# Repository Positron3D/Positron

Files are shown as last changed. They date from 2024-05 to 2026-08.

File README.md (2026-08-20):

  

<p align="center">
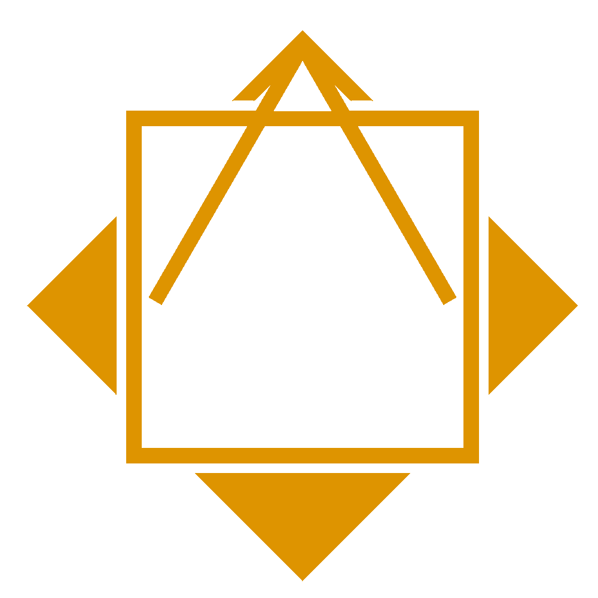
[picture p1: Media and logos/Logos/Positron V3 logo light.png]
   
</p>

---
# Positron V3.2.2
Designed by The Positron Team and LDO, the Positron V3.2 is the release version of the original Positron V3 design originally by Kralyn.

## The Positron Team
The Positron Team was founded by Kralyn and TheNomad after the release of the original Positron V3. Our team has worked closely with LDO to improve upon the original V3 design to make the entire unit more reliable, easier to assemble, and have a more elegant design as a whole.

## What is Positron
Positron is designed to be an ultra-portable printer. We have succesfully brought The Positron through major US International Airports without issue from TSA, the portability allows this printer to be easily brought along to any major event, remote workshop or maker space, job site, etc. If you have a need to bring a printer with you, The Positron may be the right printer for you.

## Why Positron?
As mentioned, we wanted an ultra-portable printer while we were in University. While travelling between our dorm and workshops, we often found the desire to bring our Printer with us, since we knew our own printers better than the community ones in the university.

We created the original V3 to achieve this goal, using what parts we had available to us at University. Then, when LDO reached out to us, we attempted to make the original V3 a production kit, but things that worked for our little team in University, didn't quite work out for mass production. As such, we spent 2 years working closely with LDO to make The Positron V3.2, an easy to assemble varient that is far more reliable for mass production.

We are extremely proud of this release, and we cannot wait for people to get their hands on the machines.

# Resources

### Klipper Configuration Files
The most up–to–date Klipper configuration files for setting up or updating the Positron are now in our [config repository](https://github.com/Positron3D/PositronConfig).
<!--#TODO: Remove "now" a few weeks after merge-->

### Mainboard / Daughterboard Schematics
For wiring & pin references, please see [LDO's Positron Hardware Repo](https://github.com/MotorDynamicsLab/PositronHardware/tree/master/PositronV3.2).

# Licenses


If you are manufacturing this 3D printer or a close derivative, please put `Positron Logo` visibily on your product and designate `Positron3D` as the inventor of this product. You can find the file inside the logos folder.

On any online postings for any Parts or Kits, please be sure to link back to this github page, as well as to Positron 3D's website.
`https://github.com/Positron3D/Positron`
`https://positron3d.com/`

If you made a profit from this design, please consider donating a portion to `Positron3D`. We will be exceedingly grateful.

***All hardware materials and designs provided here are licensed under the [CC-BY-SA-4.0](https://creativecommons.org/licenses/by-sa/4.0/) hardware license.
All documentation, including the Wiki, is under the Creative Commons [CC-BY-SA-4.0](https://creativecommons.org/licenses/by-sa/4.0/) license***.

<div align="center">
Open Licenses
</div>

## Exceptions to CC BY-SA 4.0 for LDO Motors – Positron 3D PCBs

The Positron 3D Team grants an exception to the CC BY-SA 4.0 license for PCBs developed for the Positron 3D printer and manufactured by LDO Motors under the following conditions:
1. Limited Scope: This exception applies only to PCB designs developed by the Positron 3D Team and manufactured by LDO Motors. All other components remain under CC BY-SA 4.0.
2. No ShareAlike Requirement: Modifications or derivatives of these PCBs do not need to be shared under CC BY-SA 4.0.
3. Commercial Use Restriction: Manufacturing and resale of these PCBs are limited to LDO Motors and authorized distributors. Personal, non-commercial use is permitted.
4. Attribution Requirement: Any use of these PCB designs must credit Positron 3D Team and LDO Motors per CC BY-SA 4.0.
5. No Warranty: The Positron 3D Team and LDO Motors provide the PCBs as-is, with no guarantees. Users assume all risks.

This exception ensures manufacturing consistency while maintaining open-source principles. For licensing inquiries, contact Positron 3D Team or LDO Motors.

[Top](#positronv3)

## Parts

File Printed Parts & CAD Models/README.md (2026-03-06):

# Before Printing - CALIBRATION
ABS and similar materials are prone to shrinking, changing the dimensions of the printed part from the original design.  If you have too much shrinkage, holes may not line up for screws, and parts may interfere with others.

We strongly recommend first printing the Calibration Test piece `calibration_test_100x30mm.stl` (Printed Parts & CAD Models\Calibration\) at 100% scale in the recommended print settings.

Measure the printed part (ideally with at least inexpensive calipers).  The part should be as close to 100mm in length and 30mm in length as possible.  

Adjust the scale in the slicer until the printed part measures 100mm in length and 30mm in width.  **Use this updated scale for the rest of the printed parts.**

example: Printing the calibration piece at 100.5% yields a measured printed part of 100x30mm; use 100.5% to scale all other printed parts by X/Y/Z in the slicer.

NOTE: The 3mf files in the **\#Pre-Sliced Plates folder** default to 101% scale.  This may or may not be appropriate for your printer!  Select all the parts and change the scale to the scale percentage you determined above before slicing.

# Version
Current Release Printed Parts = Positrion V3.2.2 (includes LDO Batch 3; current as of 2026-03-06).

# Directory
## CAD Files
Exactly what it says - these are the CAD files of the Positron V3.2

## Current Release Printed Parts
If you wish to build a stock Positron, this is how you do it.

## Experimental Release Printed Parts
These are various parts in the stage of testing, we are experimenting with these as potential Release Candidates.

If testing goes well, these will likely be adopted as official design revisions.

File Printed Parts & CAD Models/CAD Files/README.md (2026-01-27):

# Updated 2026-01-26
The CAD files have been cleaned up, color/material assigns in the Fusion files (f3d).  All subassemblies have been re-organized and re-exported into the Subassemblies folder.

The files have a _YYYY-MM-DD suffix noting the date of export.

# Live (Web) CAD Viewer
The initial LDO Kit Release Live Fusion Model can be [viewed here](https://a360.co/4dAXmJX) (2024-08-23 version).

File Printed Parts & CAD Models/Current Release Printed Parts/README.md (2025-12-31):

# Positron v3.2 Printed Parts
Hello - all of these folders are what is required to build your Postiron.

In each folder, you will find a readme, this will act as a general Key for the naming of the files, as well as a spot where we've added advisories for some parts. This is as simple as informing you if a part will not be seen from the exterior, if a part will be closely intact with a high temperature item such as a motor, or if a part is recommended to be non-conductive for electrical isolation.

Please note that the folders here are grouped by assembly, and not by recommended order of assembly. Please be sure to follow the guides provided on our wiki.

# Material needed
 - 198.51g for Primary
 - 170.57g for Accent

# Recommended Print Settings

 - We recommend printing all parts in ABS or ASA
 - [We're copying Voron's homework;](https://docs.vorondesign.com/sourcing.html#print-settings)
    - Layer height: 0.2mm
    - Extrusion width: 0.4mm
    - Infill percentage: 40%
    - Infill type: grid, gyroid, honeycomb, triangle, or cubic
    - Wall count: 4
    - Solid top/bottom layers: 5
    - Supports: NONE

ABS or ASA is the recommended filament for most parts, PLA and PETG can be used for accent pieces, but please only do so at your own discretion.

## Important Note
These files are not pre-scaled as modern slicers have a shrinkage factor built in, please be sure to scale your parts accordingly. If you are unsure, try scaling parts by 100.5%

# Example Renders
Below are renders we generated. For reference between "Primary" and "Accent" colors;
 - Primary Colors; Extruder, Panels, Main Hotend Body
 - Accent Colors; Control Panel, Vents, End Caps.
 - Any Colors; Non visible parts that will not be seen in the final build.

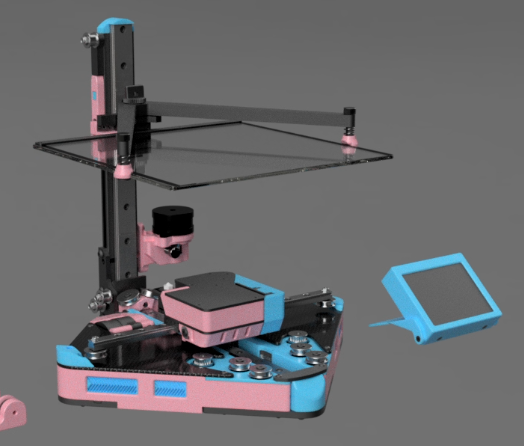
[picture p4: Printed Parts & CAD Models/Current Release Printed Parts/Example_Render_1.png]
Example Render 1

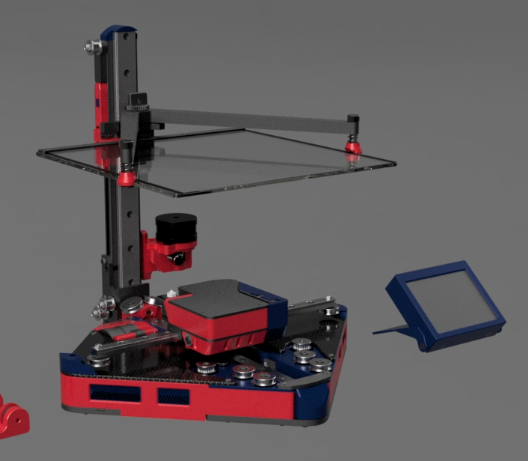
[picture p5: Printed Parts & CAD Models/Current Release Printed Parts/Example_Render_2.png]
Example Render 2

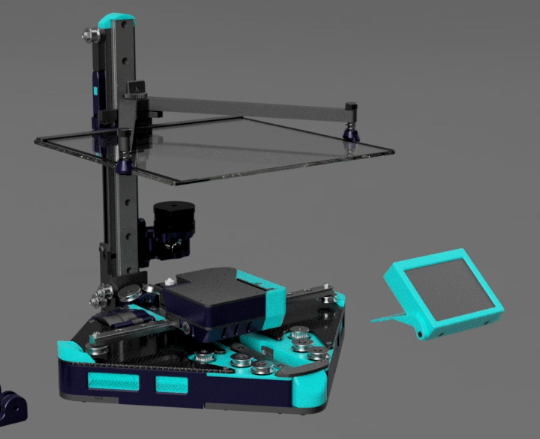
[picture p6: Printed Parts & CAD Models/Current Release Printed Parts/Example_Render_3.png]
Example Render 3


# FILE NAME KEY:
`Part Name - Quantity - Recommended Color - Notes`

### Example 1;
`Bed_Cable_Guide - 1x - Accent`  

This is the `Bed_Cable_Guide`, you need to print One of them, recommended in an accent color.

### Example 2;
`Z_PCB_Spacer - 1x - Any - Non-Conductive`

This is the `Z_PCB_Spacer`, you need to print One of them, you can use any color, and must not be conductive.

# Questions or Comments
Please feel free to join our [Discord](https://discord.gg/positron) to help with any feedback. We appreciate any and all feedback that can help us better improve our designs.

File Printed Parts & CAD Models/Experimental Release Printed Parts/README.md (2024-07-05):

# Experimental Printed Parts
## What are Experimental Parts
Experimental Parts are parts that The Positron team is looking to implement as a full update, replacement, or change to the overall design.

Experimental Parts are in the process of being tested by any and all volunteers who wish to participate.

The participation of Experimentations are tracked in the Discord.

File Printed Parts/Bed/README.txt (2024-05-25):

KEY:
Part Name - Quantity - Recommended Color - Minimum Material Type - Notes

Example 1;
Bed_Cable_Guide - 1x - Accent - PLA

This is the Bed_Cable_Guide, you need to print One of them, recommended in an accent color, and at the minimum in PLA.

Example 2;
Z_PCB_Spacer - 1x - Any - ABSorASA - Non-Conductive

This is the Z_PCB_Spacer, you need to print One of them, you can use any color, at the minimum in ABS or ASA, and must not be conductive.

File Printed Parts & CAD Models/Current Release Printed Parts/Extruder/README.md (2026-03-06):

# IMPORTANT FOR THIS FOLDER

These are the printed parts for the original / OLD Extruder v1.  The [LDO Assembly Guide](https://ldomotion.com/guides/1---positron-v32---extruder) currently shows the instructions for this.

We do strongly suggest instead using the v2 Extruder if possible.  It is substantially more reliable and performant.

An assembly guide for the Extruder v2 is in progress, but you may find it helpful to use the [Positron3D CAD Viewer](https://cad.positron3d.com/?model=Positron_v3.2.2) and expand into the Extruder_v2 to see how it goes together.

## BOM
All needed parts are included with the LDO Positron Kit (there are plenty of extra fasteners):
- M2x10 Self Tapping Screw (Quantity: 2)
    - Used to attach the Z Endstop Switch to the `extruder_v2_main_body`)
- M3x25 BHCS (Quantity: 3)
    - 1x goes from the bottom through `extruder_v2_bottom_plate` and `extruder_v2_main_body` into a M3x5x4 Heatset Insert in `extruder_v2_motor_plate`.
    - 2x go through the bottom of `extruder_v2_main_body` into the LDO Pancake Stepper.
- M3x8 BHCS (2x)
    - 2x go through the bottom of `extruder_v2_bottom_plate` into M3x5x4 Heatset Inserts in `extruder_v2_main_body_*`.
- M3x5x4 Heatset Insert (Quantity: 4)
    - 1x goes into the bottom of `extruder_v2_motor_plate` (see above).
    - 2x go into the bottom of `extruder_v2_main_body_*` (see above).
    - 1x goes into the side of `extruder_v2_guidler`.
- M4 Hex Nut (Quantity: 2)
- M4x10 BHCS (Quantity: 2)
- EITHER: M3x35 SHCS or M3x35 BHCS OR the silver M3 Thumbscrew (see note below) (Quantity: 1)
    - This goes through the spring, through the washer, and into the front of `extruder_v2_main_body` and into the M3x5x4 Heatset Insert on `extruder_v2_guidler` as the tensioning mechanism.
- Extruder BMG Spring
- Washer

## Extruder Main Body Notes!
There are two versions for this part:  

Option A)
If you would like to use a M3x35 SHCS (Socket Head) or M3x35 BHCS (Button Head) as the tension fastener, use the `extruder_v2_main_body_m3x35.stl`.  Once tension is set, it generally never needs adjustment, so the smaller form factor is nice.

Option B)
If you would like to use the Silver M3 Thumbscrew supplied in the LDO Kit (originally used with the old Extruder V1), use `extruder_v2_main_body_m3thumbscrew.stl`.

Print information for the new Extruder v2 is found below:

## Colors and Naming
You will see two options;
1. If there is a `[a]` at the start of the filename, this denotes it can be printed with an accent color
    - This is a secondary, often complimentary color, and will help your build pop.
2. If there is no prefix at the start of the filename, this denotes it can be printed with the main color
    - This is the majority of the parts of the build.

Of course, these are just color coordination suggestions, please experiment and have fun!

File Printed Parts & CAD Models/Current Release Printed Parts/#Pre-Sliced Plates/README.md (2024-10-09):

# Pre-Sliced Plates
Hey, these plates aren't updated as often as the other folders are.

While these are here for convenience, we ask that you read through the other folders and update your parts accordingly.

Thank you.

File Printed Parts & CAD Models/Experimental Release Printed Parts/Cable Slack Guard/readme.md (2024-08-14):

# Cable Chain Experiment
We understand that some users have had issues with the Cables and Bowden getting caught on the X Rail during prints. 

This can be printed in anything, and has been tested without issue with PLA.

This uses the heatset insert that the original Bowden Guide, and the original screw to attach it.

# Printing
Default Strength Profiles work well for this, must use a 0.4 nozzle and be able to print walls that are 0.5mm thin.

# Assembly

Insert the heatset insert to the Toolhead Holder, and screw that into the Toolhead.

Slide the Links onto Bowden Tube, and place the XT30 cable into the clip side.

Lock the clips in, and push in the Band. This will secure the clips and will ensure they don't open.

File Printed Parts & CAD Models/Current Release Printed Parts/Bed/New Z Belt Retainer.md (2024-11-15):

# New Z Belt Retainer
Insert Two M3x10 SHCS into the back of the block, this is for added strength.
    - Not through the screw holes that go all the way through the block
Attach to the Z Carriage as normal

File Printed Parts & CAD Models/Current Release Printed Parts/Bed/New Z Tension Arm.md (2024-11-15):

# Z Tension Arm Assembly
This is now the default for Batch 3 forward. If you have a Batch 1 or 2 kit, you have all the parts to build this.

# General Instruction/Notes
M3 10mm OD washer and M3x12 BHCS or a wafer head for the pivot.
The previously used M4x10 BHCS and an M4 hex nut for the stop.
Place the ball bearing in the Z_Tension Arm, followed by the spring
Use an hex driver to compress the spring towards the ball bearing, and slide in the Tension Plug.

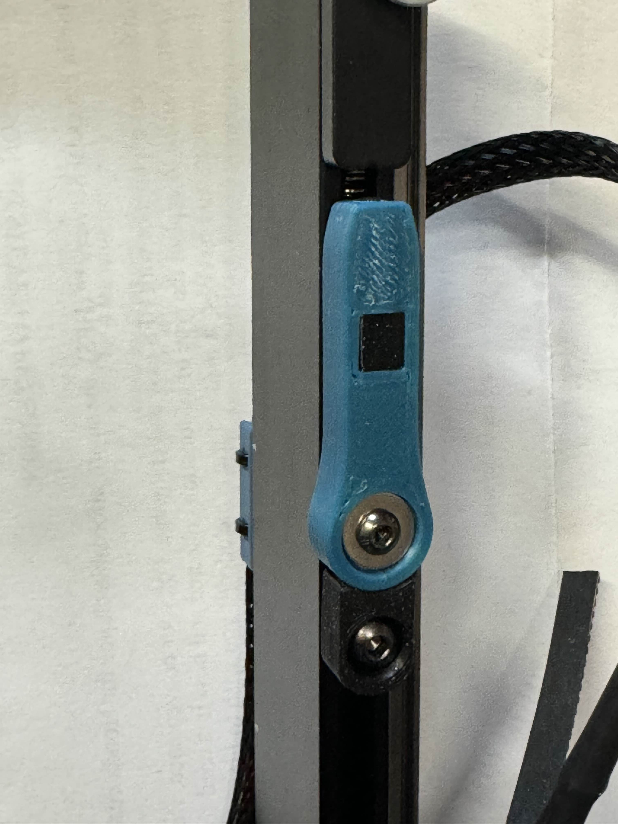
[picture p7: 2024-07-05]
Printed Parts & CAD Models/Current Release Printed Parts/Bed/New Z Tension Arm.jpg

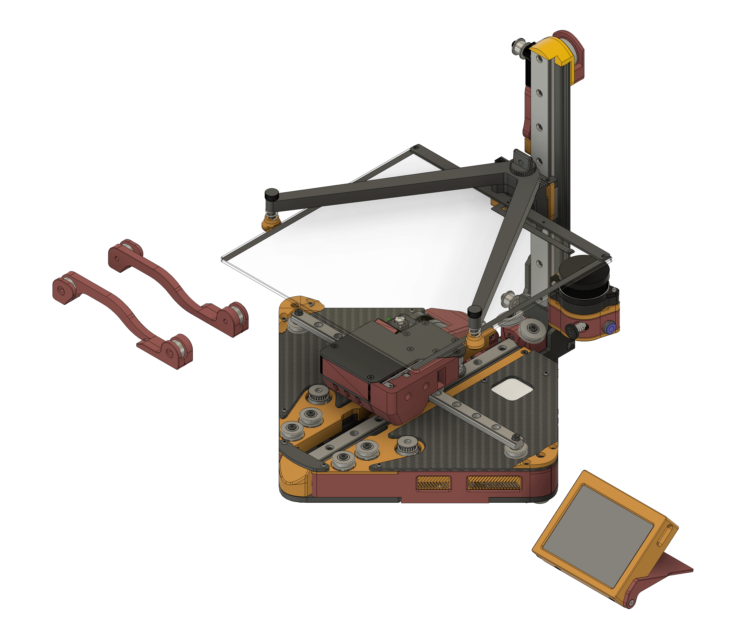
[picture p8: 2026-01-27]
Printed Parts & CAD Models/CAD Files/PositronV3.2.2_2026-01-26.png

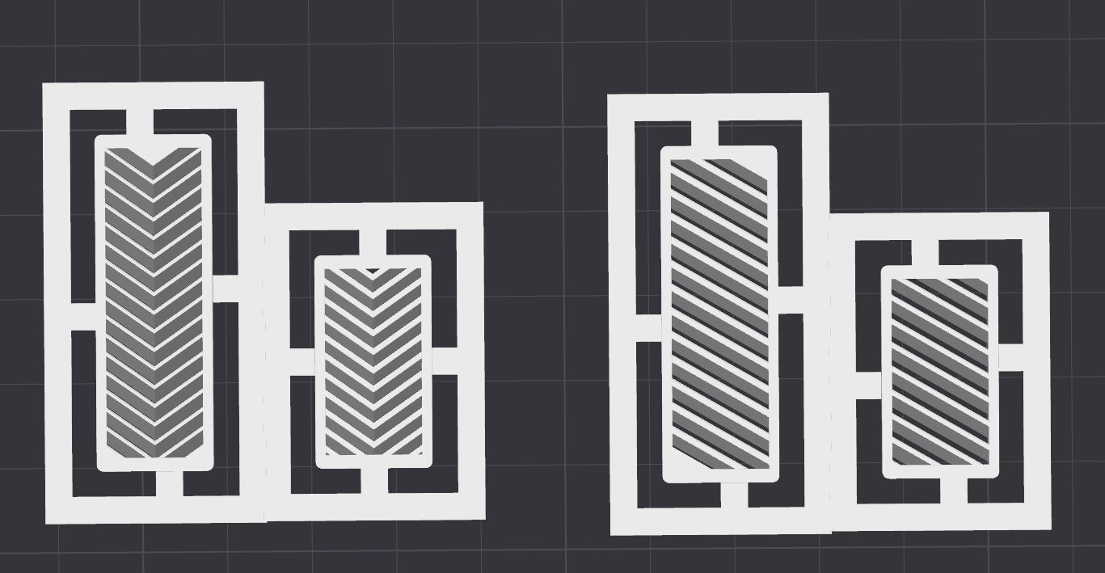
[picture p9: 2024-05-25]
Printed Parts & CAD Models/Current Release Printed Parts/Panels/Vent Grills/Style_Compare.png

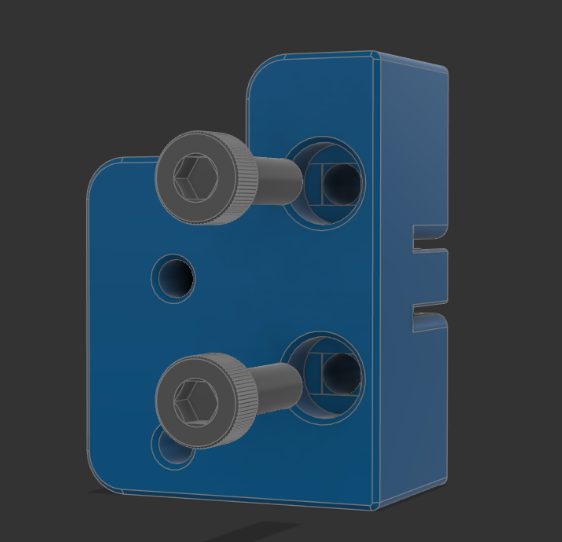
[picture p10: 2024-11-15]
Printed Parts & CAD Models/Current Release Printed Parts/Bed/Z_Belt_Retainer - Added M3x10.png

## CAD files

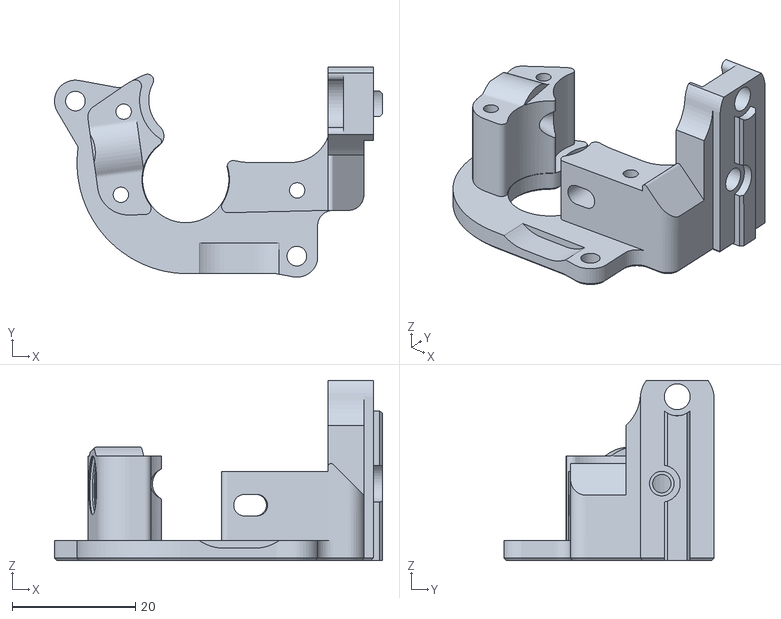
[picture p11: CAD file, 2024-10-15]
Printer Mods/Extruder - Threaded Bowden Coupler/M10 Bowden Coupler/Extruder_Main_Body - 1x - Primary - M10 Bowden - V1.1.stl
53.2 x 34.1 x 29.2

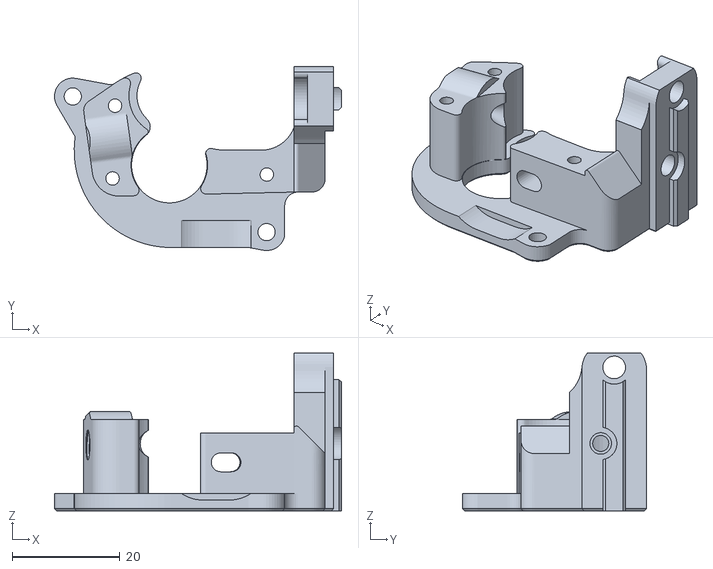
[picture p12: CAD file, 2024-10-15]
Printer Mods/Extruder - Threaded Bowden Coupler/M6 Bowden Coupler/Extruder_Main_Body - 1x - Primary - M6 Bowden - V1.1.stl
53.2 x 34.1 x 29.2

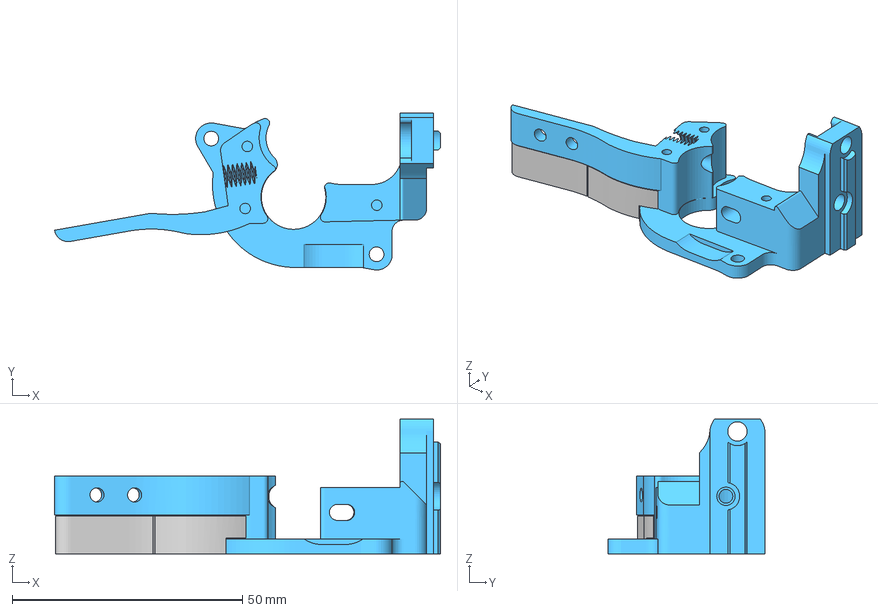
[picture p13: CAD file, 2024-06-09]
Printer Mods/Cable Chain Mod/Extruder Main Body - Cable Chain - V0.1.3mf
83.9 x 34.1 x 29.3 mm
Extruder Main Body
Included Support (1)
Included Support

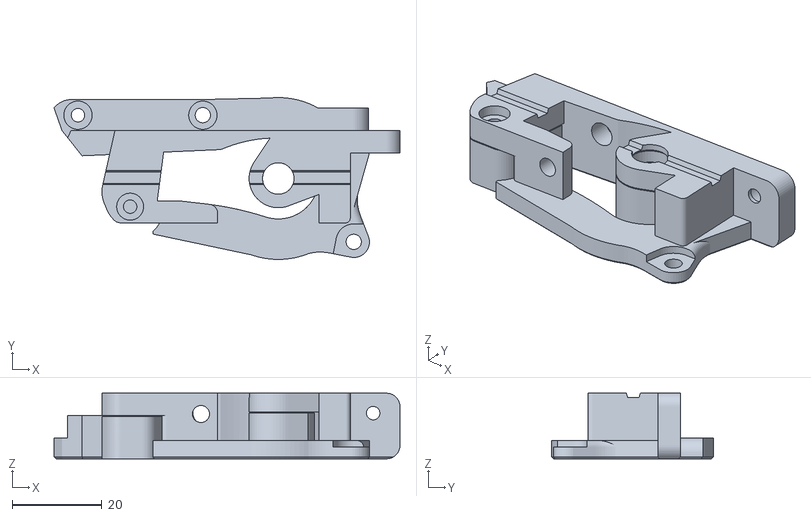
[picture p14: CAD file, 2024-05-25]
Printed Parts & CAD Models/Current Release Printed Parts/Z Drive/Z_Drive_Main_Body - 1x - Primary - HS - V1.0.stl
76.9 x 36.0 x 14.6

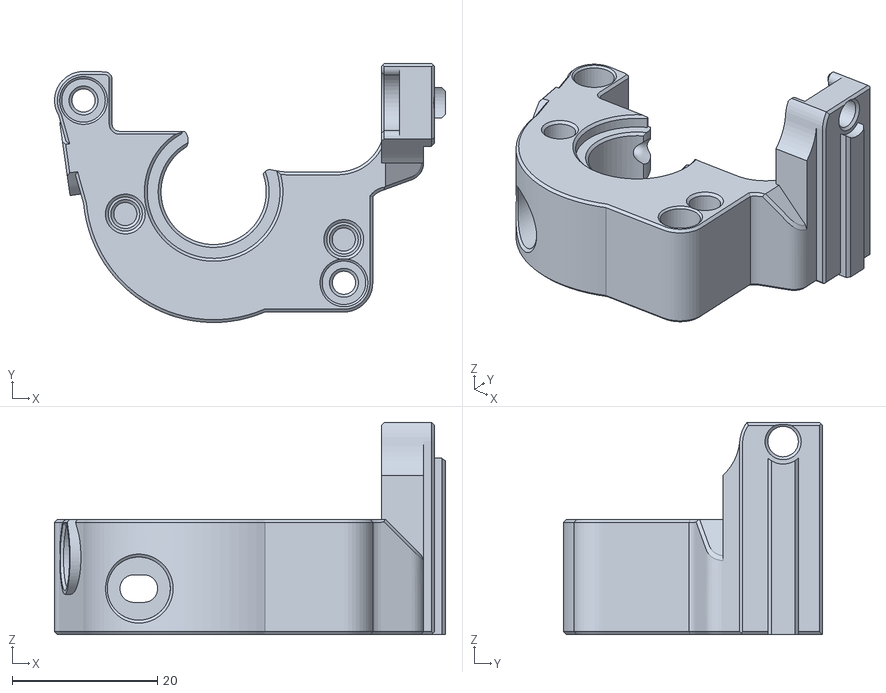
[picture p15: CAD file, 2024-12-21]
Printed Parts & CAD Models/Current Release Printed Parts/Extruder/extruder_v2_main_body_m3x35.stl
53.9 x 35.7 x 29.3

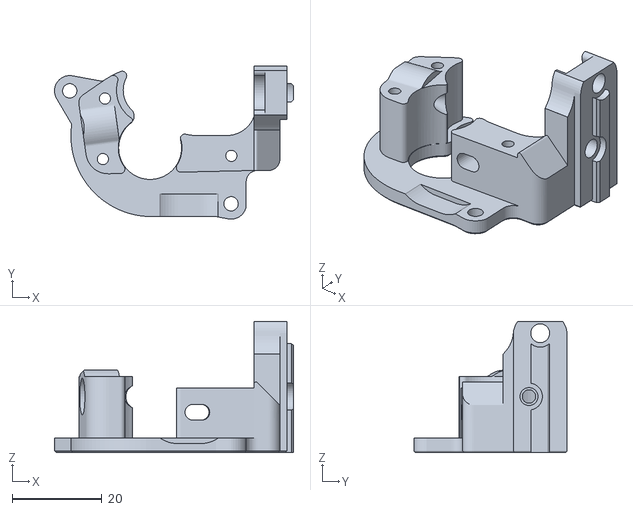
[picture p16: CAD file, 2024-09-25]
Printed Parts & CAD Models/Current Release Printed Parts/Extruder/Extruder_Main_Body - 1x - Primary - V1.1.stl
53.2 x 34.1 x 29.2

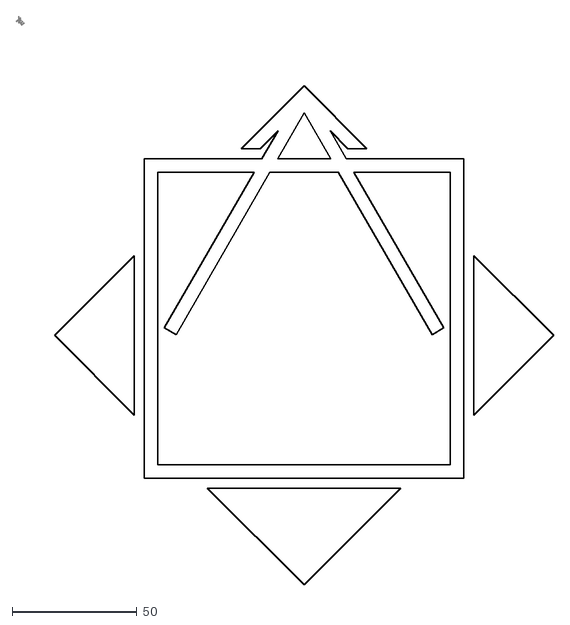
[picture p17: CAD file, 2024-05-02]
Media and logos/Logos/Positron V3 Logo v2.dxf
214.9 x 227.5

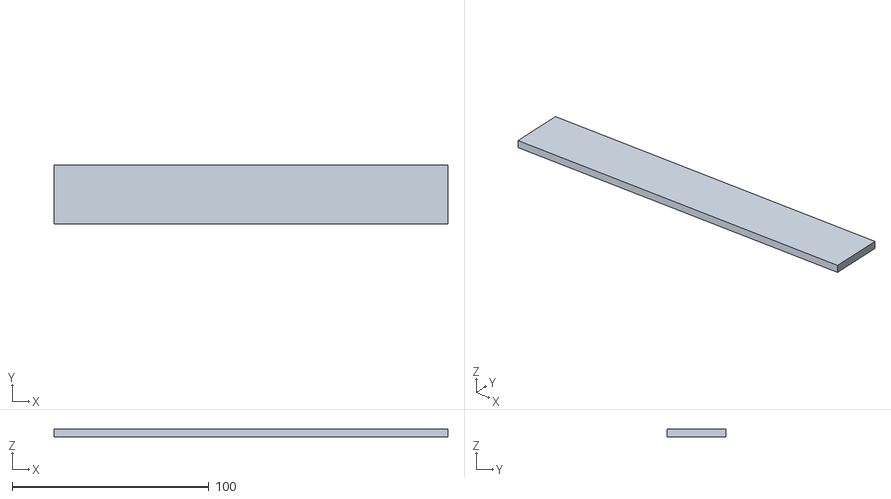
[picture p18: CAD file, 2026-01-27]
Printed Parts & CAD Models/Calibration/calibration_test_200x30mm.stl
200.0 x 30.0 x 4.00

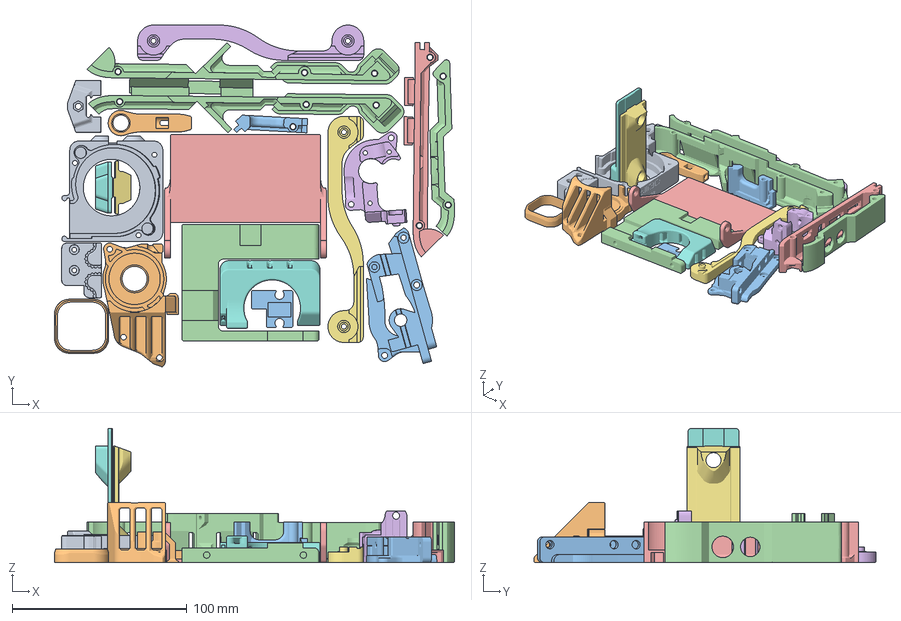
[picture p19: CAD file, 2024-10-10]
Printed Parts & CAD Models/Current Release Printed Parts/#Pre-Sliced Plates/PrusaMK4S-PRIMARY-ASA.3mf
228.6 x 195.5 x 76.8 mm
Z_Belt_Retainer_Alternative.stl
Z_Tension_Arm.stl
Z_PCB_Spacer - 1x - Any - Non-Conductive - V1.0.stl
Back_Plate - 1x - Primary - Non Conductive - HS - V1.0.stl
Cover_Stand - 1x - Primary - V1.0.stl
Extruder_Main_Body - 1x - Primary - V1.1.stl
Light_Bar_Bracket_Front - 1x - Any - V1.0.stl
Light_Bar_Bracket_Rear - 1x - Any - V1.0.stl
Rear_Idler_Tensioner_Block - 1x - Primary - HS - V1.0.stl
LED_Cluster_Retainer - 1x - Any - Heat Warning - V1.0.stl
Rear_Cable_Panel - 1x - Primary - HS - V1.0.stl
Side_Panel_Back_Left - 1x - Primary - HS - V1.0.stl
Side_Panel_Back_Right - 1x - Primary - HS - V1.0.stl
SpoolHolder_B - 2x - Primary - V1.0.stl x 2
Toolhead_Belt_Retainer_Block - 1x - Primary - HS - V1.0.stl
Part_Fan_Enclosure_Alt - 1x - Primary - HS - V1.3 - Olli3D - Housing.stl
Z_Drive_Outer_Housing - 1x - Primary - HS - V1.1.stl
Z_Drive_Main_Body - 1x - Primary - HS - V1.0.stl
Merged

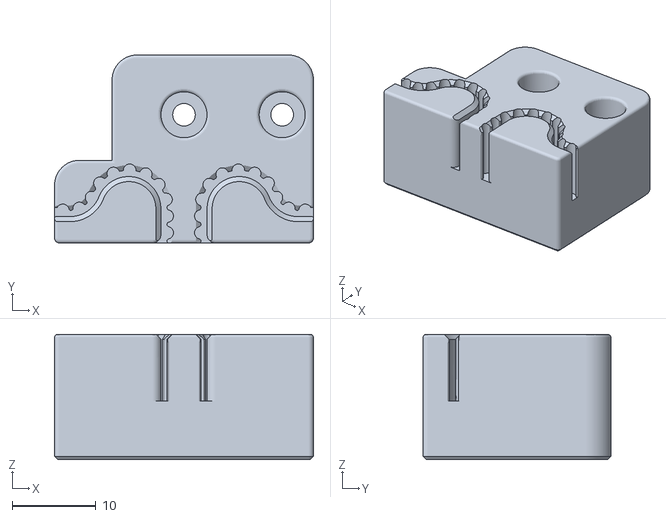
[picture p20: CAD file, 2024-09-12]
Printed Parts & CAD Models/Current Release Printed Parts/Bed/Z_Belt_Retainer - 1x - Primary - V1.3.stl
31.0 x 22.5 x 15.0

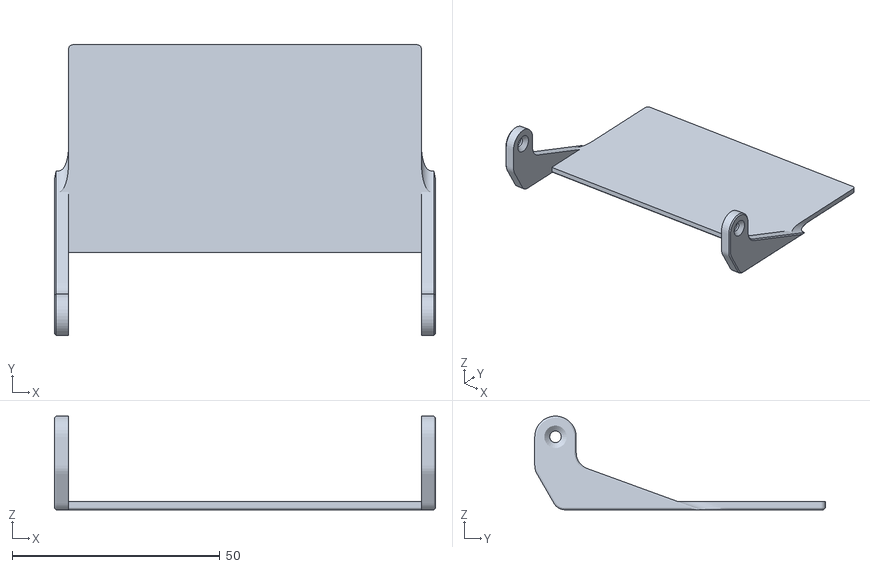
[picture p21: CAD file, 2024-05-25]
Printed Parts & CAD Models/Current Release Printed Parts/Controller/Cover_Stand - 1x - Primary - V1.0.stl
91.8 x 70.0 x 22.6

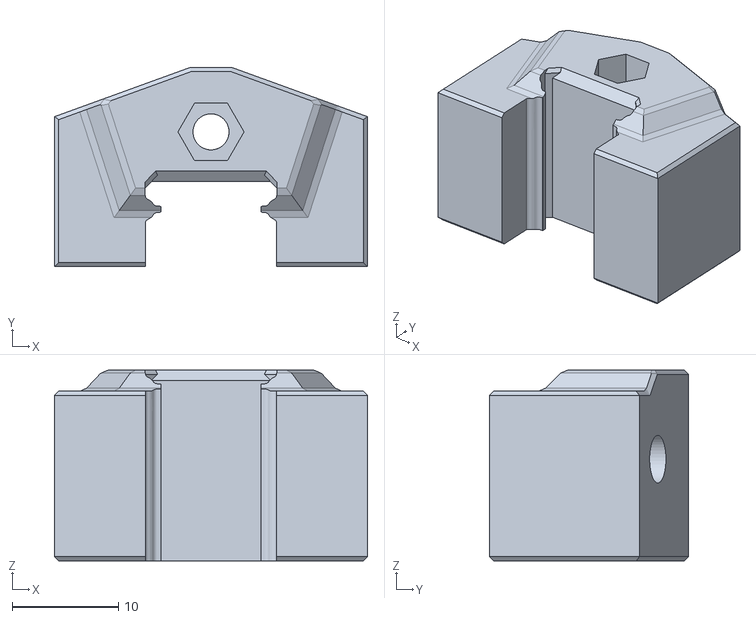
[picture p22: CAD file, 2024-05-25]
Printed Parts & CAD Models/Current Release Printed Parts/Motion/Rear_Idler_Tensioner_Block - 1x - Primary - HS - V1.0.stl
29.5 x 18.8 x 18.0

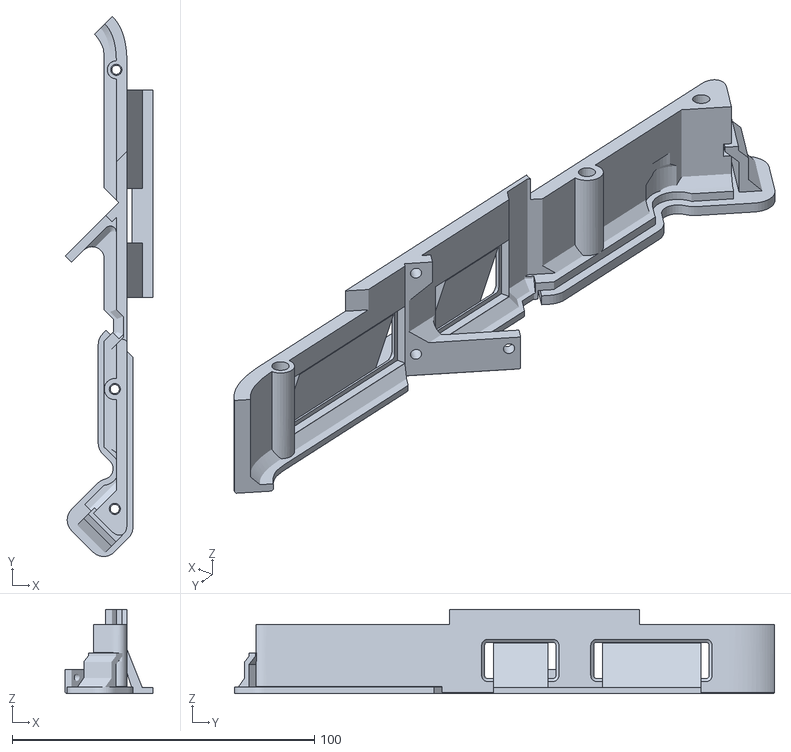
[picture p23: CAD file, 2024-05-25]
Printed Parts & CAD Models/Current Release Printed Parts/Panels/Side_Panel_Front_Left - 1x - Primary - HS - V1.0.stl
29.1 x 178.5 x 27.9

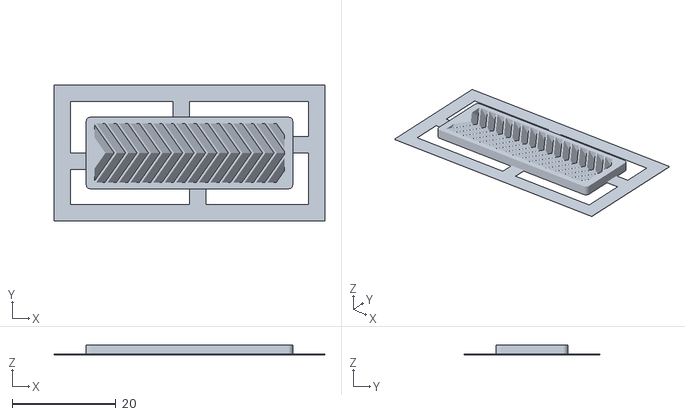
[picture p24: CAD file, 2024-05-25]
Printed Parts & CAD Models/Current Release Printed Parts/Panels/Vent Grills/Fishbone/[V]Fish_Bone_Grill_Large - 2x - Accent - V1.0.stl
52.2 x 26.2 x 2.00

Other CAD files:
Printed Parts & CAD Models/Current Release Printed Parts/Panels/Vent Grills/Slanted/[V]Slanted_Grill_Small - 2x - Accent - V1.0.stl
Printed Parts & CAD Models/Current Release Printed Parts/Panels/Vent Grills/Template Grill Frames.step
Printed Parts & CAD Models/Current Release Printed Parts/Spool Holder/SpoolHolder_C - 2x - Accent - V1.0.stl
Printed Parts & CAD Models/Current Release Printed Parts/Toolhead/Part_Fan_Enclosure - 1x - Primary - HS - V1.4 - Olli3D - Housing.stl
Printed Parts & CAD Models/CAD Files/PositronV3.2.2_2026-01-26.f3d
Printed Parts & CAD Models/CAD Files/Subassemblies/Extruder_V2_CAD.f3d
Printed Parts & CAD Models/CAD Files/Subassemblies/extruder_v2_main_body_m3thumbscrew.step
Printed Parts & CAD Models/Current Release Printed Parts/#Pre-Sliced Plates/PrusaMK4-ACCENT-ASA.3mf
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

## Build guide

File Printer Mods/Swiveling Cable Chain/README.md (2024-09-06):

# Swiveling cable chain mod

This mod adds a swiveling attachment to the extruder. This makes it possible to fold the printer
even with the cable chain still attached. The Pelican-style case that the LDO Positron ships with
can also be modified to fit the folded printer with the cable chain sticking out.

## Extra hardware required

  - 2x M2.5 BHCS 6mm bolts
  - 1x MF-148-ZZ bearings (the same type of bearing that is already in the Positron BOM)

## Printing

Print the provided STL file by splitting it into objects and rotating the pieces into the right orientation.

## Assembly

  - Push the plug through the bearing, and attach the arm that will hold the cable chain to the plug using both M2.5 6mm bolts.
  - Take this assembly and slot it into the niche for the bearing into the other two parts.
  - Possibly clear out the filament path using a 2mm drill bit, if there is anything obstructing it.
  - Assemble using the same extruder-side pieces as in the original cable chain mod.

## Photos

Open:

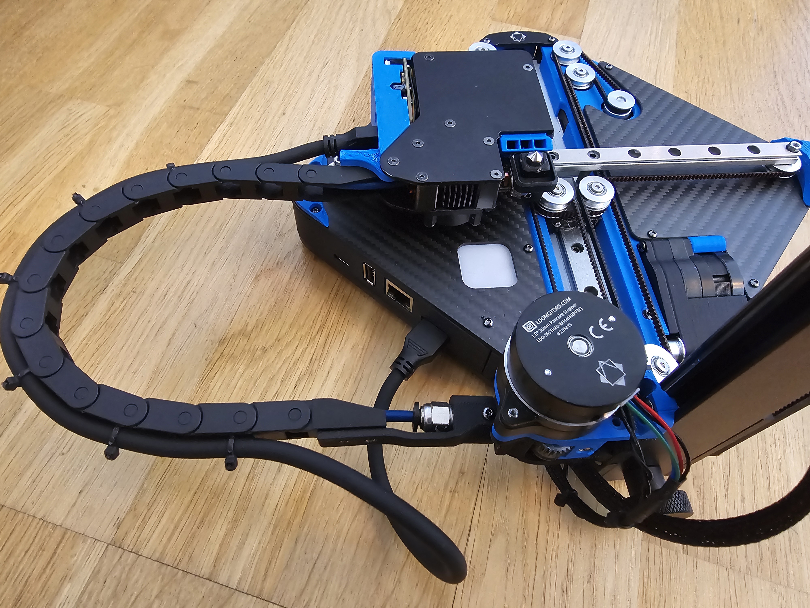
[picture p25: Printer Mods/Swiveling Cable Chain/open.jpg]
open position


Folded:

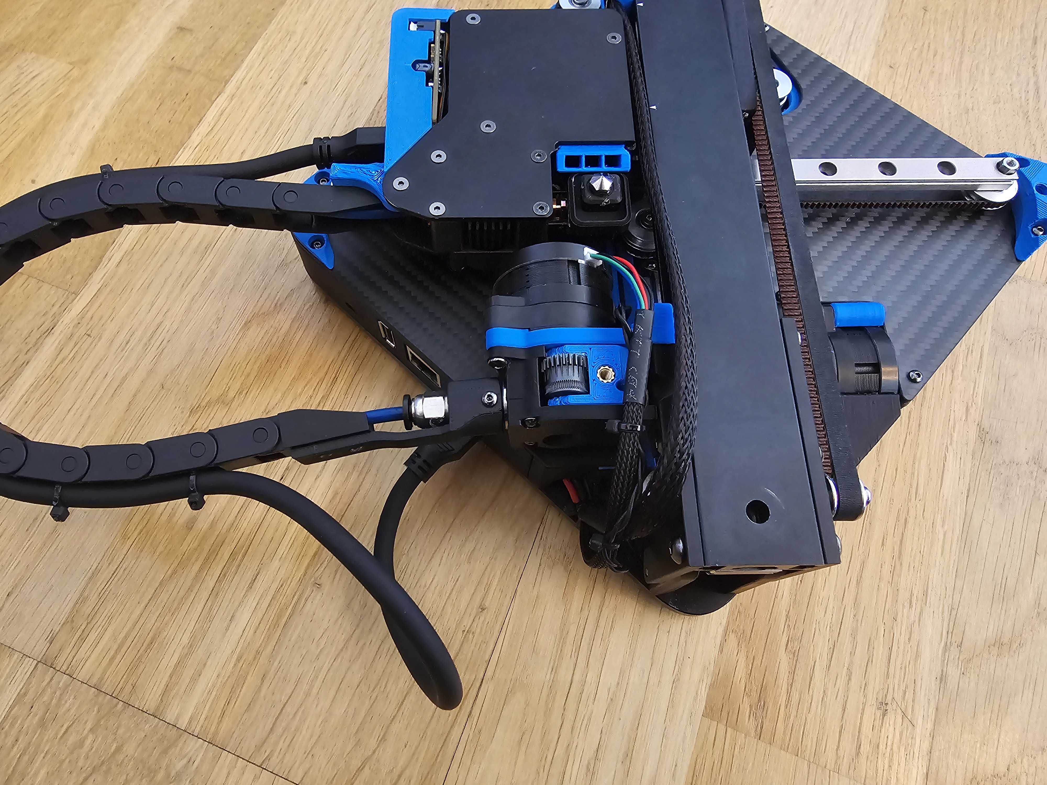
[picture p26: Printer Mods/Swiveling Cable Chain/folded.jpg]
folded positron


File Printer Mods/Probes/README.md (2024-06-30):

# Welcome to the Probes Mod Folder
No, this is not for alien abductions.

This is for any custom probe mods people wish to add to the Positron.

We have attached the first 'universal' mount system.

The current philosophy of the probe is to give the Positron a Magnetic mount of sorts for various probes.

We've included the STEP files here, and we encourage our community to build upon this, and potentially even design a method of docking probes.

Have fun.

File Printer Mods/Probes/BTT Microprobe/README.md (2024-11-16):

# Positron v3.2 - BTT Microprobe Mod
This mod allows for a Microprobe to be mounted to the Toolhead.

For Wiring reference, please see [LDO's Positron Hardware Repo](https://github.com/MotorDynamicsLab/PositronHardware/tree/master/PositronV3.2).

This mod uses some existing hardware, and mounts to the Toolhead's Heatsink. This part is very thin to allow for maximum clearance between the toolhead and the extruder. Please test your setup to ensure there is no collision.

The Servo cable is plugged into the SERVOS pins on the MCU - GPIO29

The Probe cable is plugged into the TH0 pins on the MCU - GPIO27
> Note - TH0 / GPIO27 is unused in stock configuration.

# Required Hardware
- 2x m2.5x10 for Probe Mount
- 12x 3x2mm Magnets
- 4x M2.5x6 BHCS (Included in Positron Kit)
- JST PH 2Pin Female + JST PH 3Pin Female to JST GH 5Pin Female Connector (**not** included with BTT Microprobe)

# Installation Instructions
1. Glue 6x 3x2mm Magnets into the `Probe_Heatsink_Mount`
2. Glue 6x 3x2mm Magnets into the `BTT_Microprobe Probe Harness`
3. Ensure the Magnet polarities match to allow the two parts to magnetically mount.
4. On the underside of the toolhead, remove the 4x M2.5x6 BHCS screws holding the heatsink to the bottom plate.
5. Using the screws you just removed, mount the `Probe_Heatsink_Mount` to the underside of the bottom plate, using the same holes as before.
6. Mount the BTT Microprobe to the `BTT_Microprobe Probe Harness`
7. Test and make sure the two components can magnetically couple, and decouple.

# Recommended Print Settings

 - We recommend printing all parts in ABS or ASA
 - [We're copying Voron's homework;](https://docs.vorondesign.com/sourcing.html#print-settings)
    - Layer height: 0.2mm
    - Extrusion width: 0.4mm
    - Infill percentage: 40%
    - Infill type: grid, gyroid, honeycomb, triangle, or cubic
    - Wall count: 4
    - Solid top/bottom layers: 5
    - Supports: You should be able to get away with none, but you may need a few as there are a few major overhangs.

ABS or ASA is the recommended filament for most parts, PLA and PETG can be used for many accent pieces, but please only do so at your own discretion.

# Questions or Comments
Please feel free to join our [Discord](https://discord.gg/mGDkYZtyNY) to help with any feedback. We appreciate any and all feedback that can help us better improve our designs.

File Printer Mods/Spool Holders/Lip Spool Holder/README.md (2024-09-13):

# Lip Spool Holder

A simple spool holder that replaces the Z column keystone that requires no setup, but only works with spools that have an inner lip.

It requires a M3 heatset insert and 3 × 6-10mm M3 Flat Head Socket Screws (FHSS) which can likely be sourced from spares includes with thte Positron kit. The bearing is not included, but it is a common 608 bearing commonly found in skateboards or rollerskates.

The mod is printed in two parts, flat and without supports.




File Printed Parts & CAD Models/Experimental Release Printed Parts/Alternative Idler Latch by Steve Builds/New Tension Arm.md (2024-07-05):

# Notice
This is a piece that SteveBuilds helped us redesign, we're still testing it out, but it's a bit more elegant of a design.

# General Instruction/Notes
M3 10mm OD washer and M3x12 BHCS or a wafer head for the pivot.
The previously used M4x10 BHCS and an M4 hex nut for the stop.

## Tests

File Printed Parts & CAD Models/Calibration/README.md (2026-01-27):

# Before Printing - CALIBRATION
ABS and similar materials are prone to shrinking, changing the dimensions of the printed part from the original design.  If you have too much shrinkage, holes may not line up for screws, and parts may interfere with others.

We strongly recommend first printing the Calibration Test piece `calibration_test_200x30mm.stl` (Printed Parts & CAD Models\Calibration\) at 100% scale in the recommended print settings.

Measure the printed part (ideally with at least inexpensive calipers).  Input the length of the part into the formula below to get your shrinkage scale percentage:

Scale Percentage = (200 / measured_length) * 100

Example: 
Printed calibration piece measured 198.2mm in length.
Scale Percentage = (200 / 198.2) * 100
Scale Percentage = 100.9%

**Use this updated scale for the rest of the printed parts.**

example: Printing the calibration piece at 100.5% yields a measured printed part of 100x30mm; use 100.5% to scale all other printed parts by X/Y/Z in the slicer.

NOTE: The 3mf files in the **\#Pre-Sliced Plates folder** default to 101% scale.  This may or may not be appropriate for your printer!  Select all the parts and change the scale to the scale percentage you determined above before slicing.

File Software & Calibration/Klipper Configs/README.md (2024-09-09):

## The Positron configuration files have moved: [Positron3D/PositronConfig](https://github.com/Positron3D/PositronConfig)

To help make getting the latest configs easier[^1], we've flown the Klipper configuration files over to [Positron3D/PositronConfig](https://github.com/Positron3D/PositronConfig) so you can easily download just the latest configurations without having to download the whole repository or individual files, or copy-paste the contents of the files.

We will also be able to have alternate configuration sets in the future for common mods or experimental tweaks, so stay tuned. In the meantime, happy printing^2

<p align="center">
   
</p>

[^1]: Except for this time I guess, given you're here...
[^2]: Though not on planes, only shameful printing on planes.[^9000]
[^9000]: I just figured out how to use these footnotes so I'm abusing it

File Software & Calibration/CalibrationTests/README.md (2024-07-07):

# PLEASE READ ME
This is a selection of calibration tests custom made for the Positron v3.2

# The files
## Positron_orca_BedLevel.3mf

Uses Orca Slicer with default Positron V3.2 machine settings.

This is a test file for helping with bed leveling created by joescalon.

It has been tuned for PLA, and prints by object.

First object is back center for testing z-offset.

Second and Third are front corners for testing level.

Last is the Positron Logo in the center for final level test.

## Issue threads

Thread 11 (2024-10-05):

XT30 connector loosening over time

nomadsgalaxy, 2024-10-05:
Multiple Volunteers Wanted;
Rob Volunteered
Nem Volunteered

Ideas;
Latching Design
Screwed Design
or Slot Design

Killajoedotcom, 2024-10-07:
Hell, I'll volunteer as well.

nomadsgalaxy, 2024-10-07:
> Hell, I'll volunteer as well.

Assigned - feel free to tinker. The idea is to come up with something easy to print that can lock the connector head in but be easily removed.

nomadsgalaxy, 2025-01-05:
Fix for Batch 1 & 2: https://thangs.com/designer/TechJeeper%20Designs/3d-model/Positron3D%20Toolhead%20Cover%20with%20Cable%20Clip-1236899

Batch 3 has new cable design.

Closed 2025-01-05.

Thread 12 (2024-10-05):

Bed Connector Revision (Printed Parts)

nomadsgalaxy, 2024-10-05:

smiksky, 2024-11-11:
Originally titled "Bed Connector Revision (Printed Parts)", but this isn't an issue or contribution at this point

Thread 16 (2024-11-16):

Links from LDO assembly guide lead to 404 pages

orcinus, 2024-11-16:
This is seriously unprofessional.
You can't just yank files that are actively linked by the up-to-date, web published guide.
Some of them are now moved into "old parts" folders.
Some (e.g. Z Idler Latch Plug) are seemingly completely missing.

This is ridiculous.

nomadsgalaxy, 2024-11-16:
Hi - The Positron team does not maintain the LDO guide, and we are very closely working with them to update the guide. But in order to do so, the github has to first be updated.

If you need assistance, please join our Discord, for the mentioned parts, we just announced their update last night. We'd be happy to assist with any guidance needed.

orcinus, 2024-11-16:
Thanks for the support and help.

This isn't so much about who maintains what - it's about not breaking links and managing the repo.
You can create a branch, with a "frozen" configuration, that outside resources link to, and continue working on master branch with further improvements. Or you can do the opposite - keep master frozen as a "production" branch, and keep further developments in a development branch until the ecosystem is ready for a merge.

I understand LDO is a separate team, but to my knowledge, that is the only publicly available guide you have. I hate telling people what to do and how to do it, but your team should take care of it too, not just bounce the ball back.

Also, Discord is a black hole for any open source project. Finding anything in Discord is a nightmare, it's bad for archival, it's bad for discoverability, and it's bad for pretty much anything other than discussion. It *should not* be referred to as a primary information source. Had this information been published *HERE* in the repo, instead of on Discord, this issue never would've been raised.

orcinus, 2024-11-16:
> This is admittedly part of the flawed system - We have higher priority items that must be addressed, and while our utilization of Github hasn't been optimal, it has worked fine enough. Once our higher priority items have been handled, we'll be able to look into better organizing this.

Completely understand this, and sorry for any aggressiveness.
I'm in the same situation at work at the moment, so i can empathize.

Thank you for the verbose responses and thanks for working to make the project (even) better.
It deserves it, i LOVE the concept <3

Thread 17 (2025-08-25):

Discord invite is invalid

felsgaertner, 2025-08-25:
Hello, the Discord invite on is invalid:

* Positron/Printed Parts & CAD Models/Current Release Printed Parts/README.md Line 53

Please update or renew this invite.

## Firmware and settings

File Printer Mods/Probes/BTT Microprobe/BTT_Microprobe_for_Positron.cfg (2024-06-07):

#####################################################################
#   BIQU Microprobe for Positron Mod
#
# Credit to Reed Bell (utlandr) for writing this cfg
# https://gist.github.com/utlandr/c3dab6bbcca1fc19dfc402d81cfd75e4
#
# We swapped "PROBE_DOWN" and "PROBE_UP" because it's Positron, we're inverted.
# We added "PROBE_DEPLOY" and "PROBE_RETRACT" for disambiguation too.
#
# For this to work, you will need to comment out or remove references to the IR Probe in your config.
#
#####################################################################

## --- BIQU Microprobe Klipper configuration ---
# Not much different from a standard probe config. The
# main difference compared to most probes is to disable
# deactivating the probe (PROBE_UP) after each sample
#
# You can either copy pasta this directly or import
# into your config.yml using [include biqu_microprobe.cfg]
#
# Note: if you are changing from a bltouch or one of its
# clones, remove/comment out the [bltouch] config!
# That also includes any auto generated config stored
# at the bottom by the PROBE_CALIBRATE command
#
# Note: the current control and sensor pin values are
# configured for the 'BTT SKR E3 mini V2' controller 
# board. You may need to update these values depending
# on your controller board model.
#
# Update (2023-10-17): This config is configured for
# the V1 microprobe. V2 users must update the 
# polarity of the sensor pin in the config to be 
# pull-down (^!) not pull up (^)

[gcode_macro PROBE_UP] #PROBE DEPLOY
gcode:
    SET_PIN PIN=probe_enable VALUE=1

[gcode_macro PROBE_DEPLOY]
gcode:
    SET_PIN PIN=probe_enable VALUE=1

[gcode_macro PROBE_DOWN] #PROBE RETRACT
gcode:
    SET_PIN PIN=probe_enable VALUE=0

[gcode_macro PROBE_RETRACT]
gcode:
    SET_PIN PIN=probe_enable VALUE=0


[output_pin probe_enable]
pin: gpio29  # Set to the control pin on your board
value: 0

[probe]
pin: ^!gpio27  # NOTE FOR V2 users: Set this to ^!PC14 to set the low level trigger 
deactivate_on_each_sample: False
x_offset: -17
y_offset: 0
#z_offset: 0.5  # Will be overridden when you do a PROBE_CALIBRATE
samples: 2
samples_tolerance: 0.05
samples_tolerance_retries: 3
activate_gcode:
    PROBE_UP
    G4 P500
deactivate_gcode:
    PROBE_DOWN

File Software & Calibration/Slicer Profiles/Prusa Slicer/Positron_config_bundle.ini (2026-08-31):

[printer_model:Positron]
name = Positron
variants = 0.4
technology = FFF
family = Positron
bed_model = Positron_bed.stl
bed_texture = ThePositron_bed_texture.svg
thumbnail = thumbnail_positron.png
default_materials = Jessie PLA @Positron 0.4

[print:*positron_common_04*]
arc_fitting = disabled
bottom_fill_pattern = monotonic
bottom_solid_layers = 3
bottom_solid_min_thickness = 0
bridge_acceleration = 4000
bridge_flow_ratio = 1
bridge_speed = 75
brim_separation = 0
compatible_printers_condition = printer_model=~/(Positron)/
default_acceleration = 10000
dont_support_bridges = 1
elefant_foot_compensation = 0.15
enable_dynamic_overhang_speeds = 1
ensure_vertical_shell_thickness = 1
external_perimeter_acceleration = 6000
external_perimeter_extrusion_width = 0.44
external_perimeters_first = 0
extra_perimeters = 1
extrusion_width = 0.42
fill_angle = 45
fill_density = 20%
fill_pattern = adaptivecubic
first_layer_acceleration = 1000
first_layer_acceleration_over_raft = 0
first_layer_extrusion_width = 0.48
first_layer_height = 0.2
first_layer_infill_speed = 85
first_layer_speed = 35
first_layer_speed_over_raft = 30
gcode_comments = 0
gcode_label_objects = disabled
gcode_resolution = 0.0125
infill_acceleration = 10000
infill_anchor = 600%
infill_anchor_max = 50
infill_every_layers = 1
infill_extruder = 1
infill_extrusion_width = 0.42
infill_first = 0
infill_overlap = 25%
interface_shells = 0
ironing_type = top
only_retract_when_crossing_perimeters = 0
ooze_prevention = 0
output_filename_format = {input_filename_base}_0.4n_{layer_height}mm_{printing_filament_types}_{printer_model}_{print_time}.gcode
over_bridge_speed = 75
overhang_speed_0 = 75
overhang_speed_1 = 35
overhang_speed_2 = 55
overhang_speed_3 = 110
max_volumetric_extrusion_rate_slope_negative = 0
max_volumetric_extrusion_rate_slope_positive = 0
max_volumetric_speed = 0
min_bead_width = 85%
min_feature_size = 25%
min_skirt_length = 0
overhangs = 1
perimeter_acceleration = 8000
perimeter_extruder = 1
perimeter_extrusion_width = 0.44
perimeter_generator = arachne
perimeters = 2
post_process = 
print_settings_id = 
raft_contact_distance = 0.1
raft_expansion = 1.5
raft_first_layer_density = 90%
raft_first_layer_expansion = 3
seam_position = aligned
single_extruder_multi_material_priming = 0
solid_infill_acceleration = 8000
solid_infill_below_area = 70
solid_infill_every_layers = 0
solid_infill_extruder = 1
solid_infill_extrusion_width = 0.42
spiral_vase = 0
staggered_inner_seams = 0
standby_temperature_delta = -5
support_material = 0
support_material_angle = 0
support_material_auto = 1
support_material_bottom_contact_distance = 0
support_material_bottom_interface_layers = -1
support_material_buildplate_only = 0
support_material_closing_radius = 2
support_material_contact_distance = 0.2
support_material_enforce_layers = 0
support_material_extruder = 1
support_material_extrusion_width = 0.44
support_material_interface_contact_loops = 0
support_material_interface_extruder = 1
support_material_interface_layers = 3
support_material_interface_pattern = rectilinear
support_material_interface_spacing = 0
support_material_interface_speed = 100%
support_material_pattern = rectilinear
support_material_spacing = 2.5
support_material_speed = 60
support_material_style = grid
support_material_synchronize_layers = 0
support_material_threshold = 0
support_material_with_sheath = 1
support_material_xy_spacing = 50%
support_tree_angle = 40
support_tree_angle_slow = 25
support_tree_branch_diameter = 2
support_tree_branch_diameter_angle = 5
support_tree_branch_diameter_double_wall = 3
support_tree_branch_distance = 1
support_tree_tip_diameter = 0.8
support_tree_top_rate = 15%
thick_bridges = 1
thin_walls = 1
top_fill_pattern = monotonic
top_infill_extrusion_width = 0.4
top_one_perimeter_type = none
top_solid_infill_acceleration = 6000
top_solid_layers = 4
top_solid_min_thickness = 0
travel_acceleration = 12000
travel_short_distance_acceleration = 12000
travel_speed = 420
wall_distribution_count = 1
wall_transition_angle = 10
wall_transition_filter_deviation = 25%
wall_transition_length = 100%
wipe_tower = 0
wipe_tower_acceleration = 6000
wipe_tower_cone_angle = 0
wipe_tower_extra_flow = 100%
wipe_tower_extra_spacing = 100%

[print:Positron Detail 0.12mm]
inherits = *positron_common_04*
external_perimeter_speed = 130
gap_fill_speed = 180
infill_speed = 200
layer_height = 0.12
max_print_speed = 200
perimeter_speed = 160
skirt_distance = 6
skirt_height = 1
skirts = 1
slice_closing_radius = 0.049
small_perimeter_speed = 110
solid_infill_speed = 160
top_solid_infill_speed = 130
travel_speed_z = 20

[print:Positron Standard 0.2mm]
inherits = *positron_common_04*
external_perimeter_speed = 180
gap_fill_speed = 200
infill_speed = 250
layer_height = 0.2
max_print_speed = 200
over_bridge_speed = 110
perimeter_speed = 200
small_perimeter_speed = 120
solid_infill_speed = 200
top_solid_infill_speed = 200
travel_speed_z = 0
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

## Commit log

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2024-05-04 Added Alpha Klipper Config
    [fluidd.cfg, positron_macros.cfg, printer.cfg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]
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2024-05-25 reorient stls
    Oriented stls for printability
    [WirePick - 1x - Any - PETG.stl, XYBeltClamp - 2x - Any - PETG.stl]
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2024-05-27 Update Panels README.md
    Updated LED_Cluster_Retainer to have a Heat Advisory.
    Upon recent deconstruction, we found this part is prone to minor warping if printed in PLA, as such we now recommend this part be printed in ABS or ASA.
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2024-05-29 Filename Overhaul
    All Recommendations changing to use ABS/ASA
    Added Version Numbers to all file names
    Changed READMEs accordingly.
    [AB_Pulley Alignment_Tool - 1x - Any - V1.0.stl, Back_Plate - 1x - Accent - Non Conductive - HS - V1.0.stl, Bed_Cable_Guide - 1x - Accent - V1.0.stl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]
2024-05-29 Added Positron Maker Chip
    [Positron3D Chip - Multi Material - V1.0.3mf]
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2024-06-04 Preliminary BTT Microprobe Mod
    [BTT Microprobe Mount.3mf, BTT Microprobe Mount.step, BTT Microprobe Toolboard Cover.3mf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]
2024-06-04 Updated Mod Version Names & Orientation
    [BTT Microprobe Mount - V0.1.2.3mf, BTT Microprobe Mount - V0.1.2.step, BTT Microprobe Mount.3mf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]
2024-06-05 Updated Designs for BTT Microprobe Mod
    [BTT Microprobe Mount - V0.1.2.3mf, BTT Microprobe Mount - V0.1.2.step, BTT Microprobe Mount - V0.1.3.3mf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]
2024-06-07 BTT Microprobe Continued experimentation
    [BTT Microprobe Mount - V0.1.3.3mf, BTT Microprobe Mount - V0.1.3.step, BTT Microprobe Spicy Mount.3mf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]
2024-06-07 BTT Microprobe V2 for Positron - V0.2.0
    [BTT Micro Probe Mount - V0.2.0.step, BTT Microprobe Mod Assembly - V0.2.0.step, BTT Microprobe Mount - V0.1.3.3mf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]
2024-06-09 Cable Chain mod Experimentation
    [Extruder Main Body - Cable Chain - V0.1.3mf, Toolboard Cover - Cable Chain Mod V0.1.3mf]
2024-06-09 Cable Chain Mod Extruder Update
    Made the assembly actually able to be assembled.
    Also added threads for a PC4-M10 Bowden Coupler
    [Extruder Bottom Plate - Cable Chain - V0.1.3mf, Extruder Main Body - Cable Chain - V0.1.3mf]
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2024-06-21 ALL THE STEPS
    We had to compress some assemblies into ZIP files because they were larger than 100 MB
    [A Drive Assembly.step, B Drive Assembly.step, PV3 Portable Spool Holder x2.step]
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2024-06-25 Spelling error
    [Part_Fan_Enclosure_Alt - 1x - Primary - HS - V1.0 - Olli3D - Duct.stl, Part_Fan_Enclosure_Alt - 1x - Primary - HS - V1.0 - Olli3D - Housing.stl]
2024-06-28 Bed Cable Guide now Matches LDO Release
    [Bed_Cable_Guide - 1x - Accent - V1.0.stl]
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2024-06-30 Revised the BTT Mod
    Now the mod is agnostic to the fan duct.
    [BTT Micro Probe Mount - V0.2.0.step, BTT Microprobe Mod - V0.2.0_BTT Microprobe Mount v4.stl, BTT Microprobe Mod Assembly - V0.2.0.step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]
2024-06-30 Fixed STL orientation.
    [BTT_Microprobe Probe Harness - V0.3.stl, Probe Heatsink Mount - V0.3.stl]
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2024-07-04 Minor Fixes
    [Bed_Cable_Guide - 1x - Accent - V1.0.stl, Extruder_Motor_Plate - 1x - Primary - V1.0.stl, Extruder_Motor_Plate_Endstop - 1x - Primary - V1.0.stl]
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2024-07-05 Fixed Orientations
    [Extruder_Bottom_Plate - 1x - Primary - M10 Coupler - V1.0.3mf, Extruder_Bottom_Plate - 1x - Primary - M10 Coupler - V1.0.stl, Extruder_Main_Body - 1x - Primary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]
2024-07-05 Fixed a model
    [Steves_Z_Tension_Stop - 1x - Accent - V1.0.stl]
2024-07-05 Fixed Orientation
    [Z_Belt_Retainer_Block - 1x - Primary - V1.1.stl]
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2024-07-07 Renamed Software to Software, Configs, Calibration
    As the commit header says. Renamed Software to Software, Configs, Calibration per request of Nomad.
    [PositronOrcaProfiles - V1.0.3mf, Positron_orca-BedLevel.3mf, fluidd.cfg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]
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2024-07-16 3mm belt cutting jig
    3mm belt cutting jig for this kind of razor blade https://www.uline.com/Product/Detail/H-595B/Blades-and-Dispensers/Single-Edge-Razor-Blades?id=H-595B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
    [Positron Z belt cutting jig.stl]
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2024-07-16 Rename Positron Z belt cutting jig.stl to Positron 6mm to 3mm belt cutting jig.stl
    [Positron 6mm to 3mm belt cutting jig.stl]
2024-07-17 Create Extruder_Main_Body - 1x - Primary - M6 Bowden - V1.0.stl
    [Extruder_Main_Body - 1x - Primary - M6 Bowden - V1.0.stl]
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2024-08-15 fixed sizing
    [Pre-Sliced Plates.3mf, Printable Chain - Band.stl, Printable Chain - Toolhead Holder.step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]
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2024-08-24 Remove defunct files
    The moonraker config backup is no longer applicable, and the fluidd config is a system link to a read only file updated with fluidd
    [fluidd.cfg]
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2024-09-05 Renamed "Software, Configs, Calibration" to "Software & Calibration" 😎
    [PositronOrcaProfiles - V1.0.3mf, Positron_orca-BedLevel.3mf]
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2024-09-12 STL Cleanup & Updates for Batch 2
    Mostly Minor adjustments, Batch 1 parts will still work. Added some experimental parts.
    [Edge_Connector_Alignment_Tool - 1x - Any - V1.0.stl, Edge_Connector_Alignment_Tool - 1x - Any - V1.1.stl, Push-In 1.5mm Belt Retainer.step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]
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2024-09-25 Create Extruder_Main_Body - 1x - Primary - V1.0.stl
    [Extruder_Main_Body - 1x - Primary - V1.0.stl]
2024-09-25 Create Extruder_Bottom_Plate - 1x - Accent - V1.1.stl
    [Extruder_Bottom_Plate - 1x - Accent - V1.1.stl]
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2024-10-04 Complete folder migration
    completed move of 'Printed Parts' to 'Printed Parts & CAD Models'
    [AB_Pulley Alignment_Tool - 1x - Any - V1.0.stl, Back_Plate - 1x - Accent - Non Conductive - HS - V1.0.stl, Bed_Cable_Guide - 1x - Accent - V1.0.stl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]
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2024-10-10 Update Extruder_Bottom_Plate - 1x - Accent - V1.1.stl
    Fixed print orientation
    [Extruder_Bottom_Plate - 1x - Accent - V1.1.stl]
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2024-11-15 Updated Z Assembly
    Moving officially to the parts designed by Steve Builds
    [Z_Belt_Retainer - 1x - Primary - V1.3.stl, Z_Belt_Retainer_Block - 1x - Primary - V1.0.stl, Z_Idler_Latch - 1x - Primary - V1.0.stl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]
2024-12-21 Added Incremental Updates, added V2 Extruder to independent folder.
    [Extruder_Bottom_Plate - 1x - Accent - V2.0.stl, Extruder_Guidler - 1x - Accent - HS - V2.0.stl, Extruder_Main_Body - 1x - Primary - V2.0.stl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]
2024-12-21 re-fixed orientations
    [Extruder_Guidler - 1x - Accent - HS - V2.0.stl]
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2026-03-01 Add Cad Models for V2 Extruder
    Designed By Sample Name and BioKeks,
    [Extruder_V2_CAD.f3d]
2026-03-06 Renamed Current Release to specify v3.2.2. Also added README and clarity to Extruder V2 versus the old V1.
    [AB_Pulley Alignment_Tool - 1x - Any - V1.0.stl, Back_Plate - 1x - Primary - Non Conductive - HS - V1.0.stl, Bed_Cable_Guide - 1x - Accent - V1.0.stl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]
2026-03-06 Revert directory name change -- out of scope for this PR.
    [AB_Pulley Alignment_Tool - 1x - Any - V1.0.stl, Back_Plate - 1x - Primary - Non Conductive - HS - V1.0.stl, Bed_Cable_Guide - 1x - Accent - V1.0.stl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]

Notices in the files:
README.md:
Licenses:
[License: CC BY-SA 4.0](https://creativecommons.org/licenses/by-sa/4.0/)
